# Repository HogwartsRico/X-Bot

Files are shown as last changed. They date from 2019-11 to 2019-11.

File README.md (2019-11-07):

# X-Bot
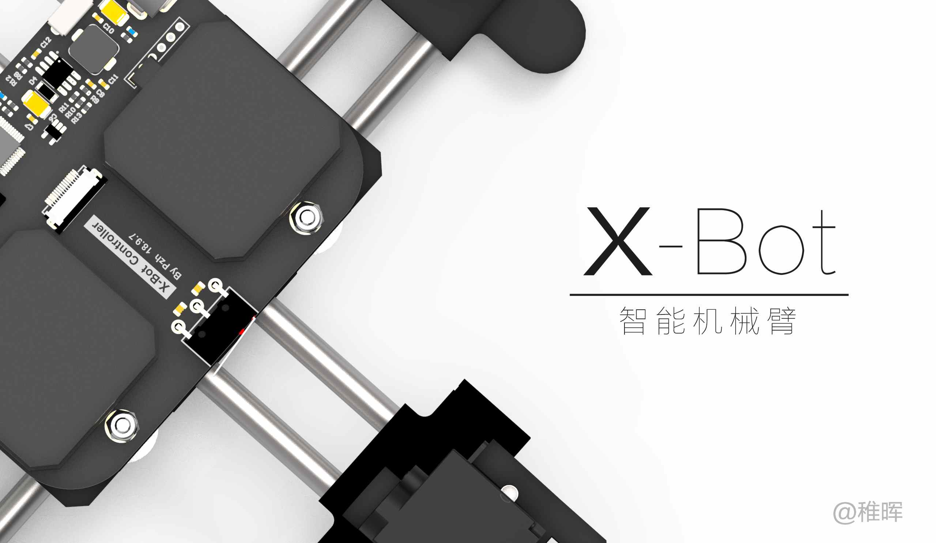
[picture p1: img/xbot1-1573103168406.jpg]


这是一个自己设计的超迷你写字机器人，软件、电路、结构完全开源。

## 前言

关于相信机械臂大家应该都了解过，小到3D打印机、激光雕刻机，大到工厂里使用的工业机械臂，都是机械臂控制的典型应用。随着工业4.0时代的到来，机械臂这样一类最典型的“机器人”，正在逐渐服务于我们生活的方方面面。

X-Bot就是这样一个机械臂作品，确切地说它是我另一个AI项目的先导作品，由于之前看paper发现一个很有趣的条件生成式对抗网络（CGAN）模型，所以产生了一些脑洞准备动手结合硬件造一个AI灵魂画手。既然是画手，光有AI算法当然还不够传神，所以X-Bot就应运而生了，当时也考虑过好几种机械臂方案，最终选择了CoreXY结构作为X-Bot的设计方案。

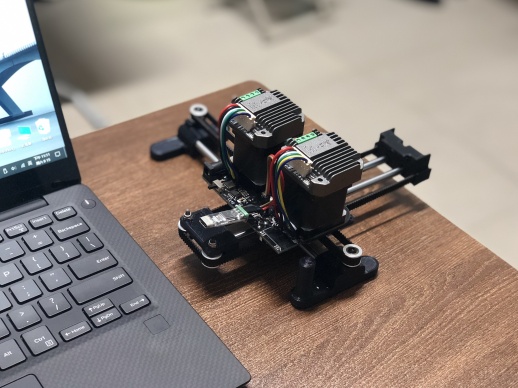
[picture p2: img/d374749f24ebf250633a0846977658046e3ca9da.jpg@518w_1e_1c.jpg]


## 关于机械臂

那么CoreXY结构是什么东西呢？

首先我们来了解一下目前比较流行的机械臂结构有哪些：

> 最经典的XYZ结构

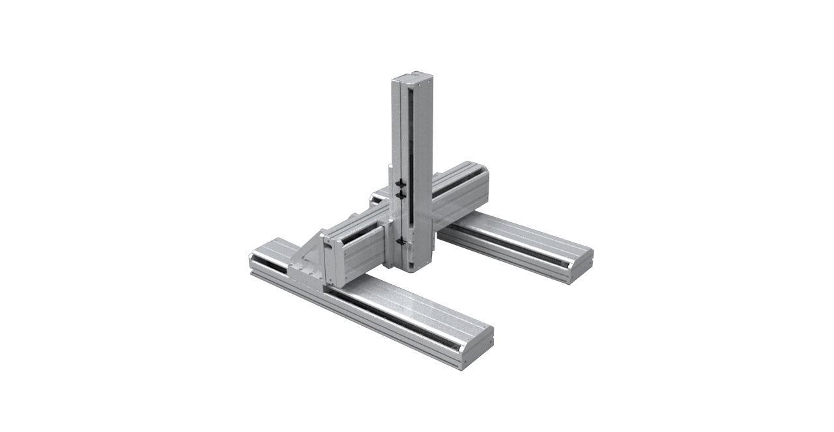
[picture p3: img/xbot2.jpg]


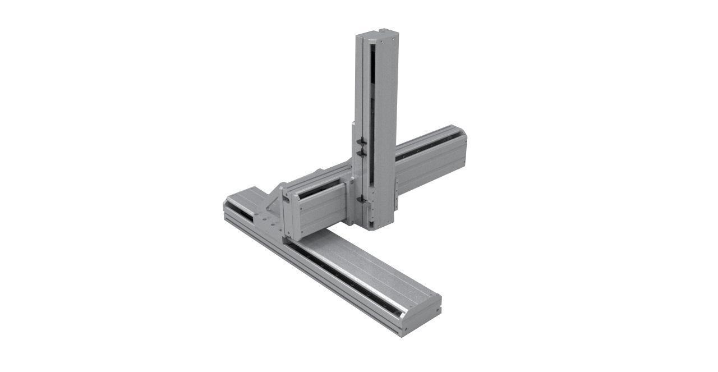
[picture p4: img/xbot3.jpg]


这一类结构大家应该一眼就能看明白是怎么回事，简单说就是在X、Y、Z三个方向上都是独立的直线运动，虽然形式有多种比如图中的第一种被称作龙门式，一般在雕刻机领域用的很多；而第二种在比较追求小型化的3D打印机上经常可以看到其身影。

XYZ结构的好处就结构非常简单，控制也很简单，由于三个方向上的运动都是解耦的（一个方向的运动不会影响到另一个方向），而且相对来说由于是纯线性驱动，其运动精度会比较容易控制。

> DELTA结构

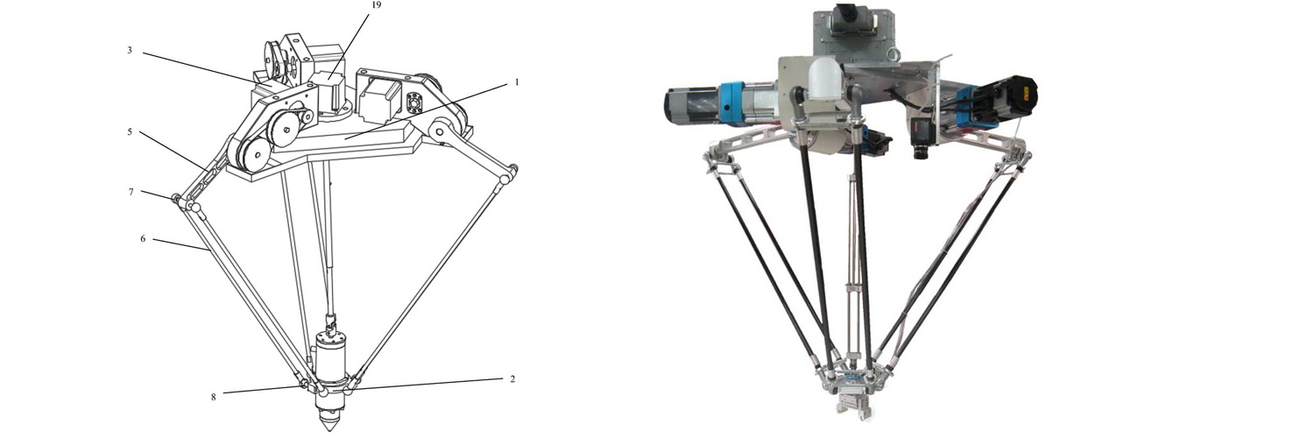
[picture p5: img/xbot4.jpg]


由于我们身处三维空间，因此来说只要是三个*线性独立*的向量都可以用来表征空间中一个唯一的坐标，对应于机械臂中，就是说只要我有三个可以精确驱动控制的电机，我就可以玩出各种花样让一个机械臂精确地运动到某一点。在XYZ结构中，X、Y、Z三个电机的地位并不是对等的，而DELTA结构则以一种很巧妙的方式完全对称地放置三个电机，如上图所示。通过三根连杆两端一共六个万向关节的约束，DELTA机械臂的末端可以运动到三维空间中的任意一点（在行程范围内，且行程空间并不是和XYZ结构一样的一个立方体），这种结构的好处就是非常的**炫酷**，哈哈，其实几年前个人最早决定设计自己的3D打印机的时候，就对DELTA结构非常的热衷~由于杠杆效应，一般来说这类机械臂的运行速度都要比XYZ要快一些，同时由于非线性控制坐标解算需要消耗更多的计算资源，有兴趣的同学可以去了解一下DELTA结构到XYZ坐标的解算公式推导过程。

> 圆柱结构

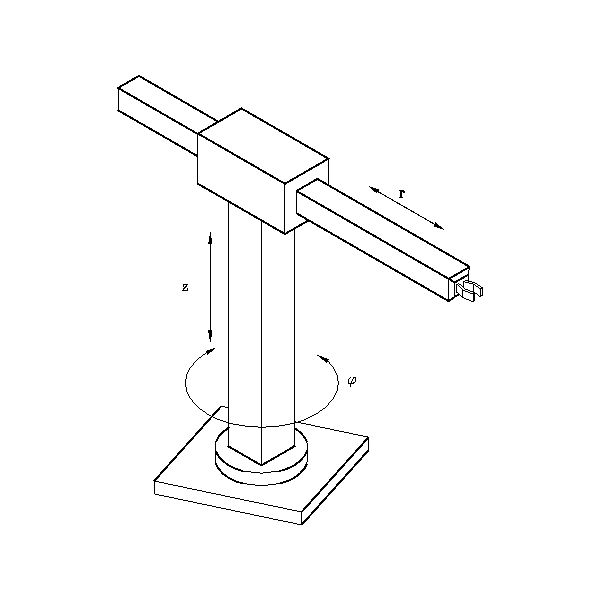
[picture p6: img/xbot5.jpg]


提到XYZ大家首先想到的是笛卡尔坐标系，然而我们在中学的时候就学过另一种坐标系叫极坐标系，也就是用一个角度和一个长度就可以表征平面内一个点的坐标，而且其跟XY坐标的转换也很方便。那么讲极坐标系再加上一个Z轴的直线运动，就得到了这样的圆柱结构机械臂。这类机械臂在实际应用中见到的比较少，因为同为极坐标结构，下面这种SCARA结构有着更“拟人”的效果。

> SCARA结构

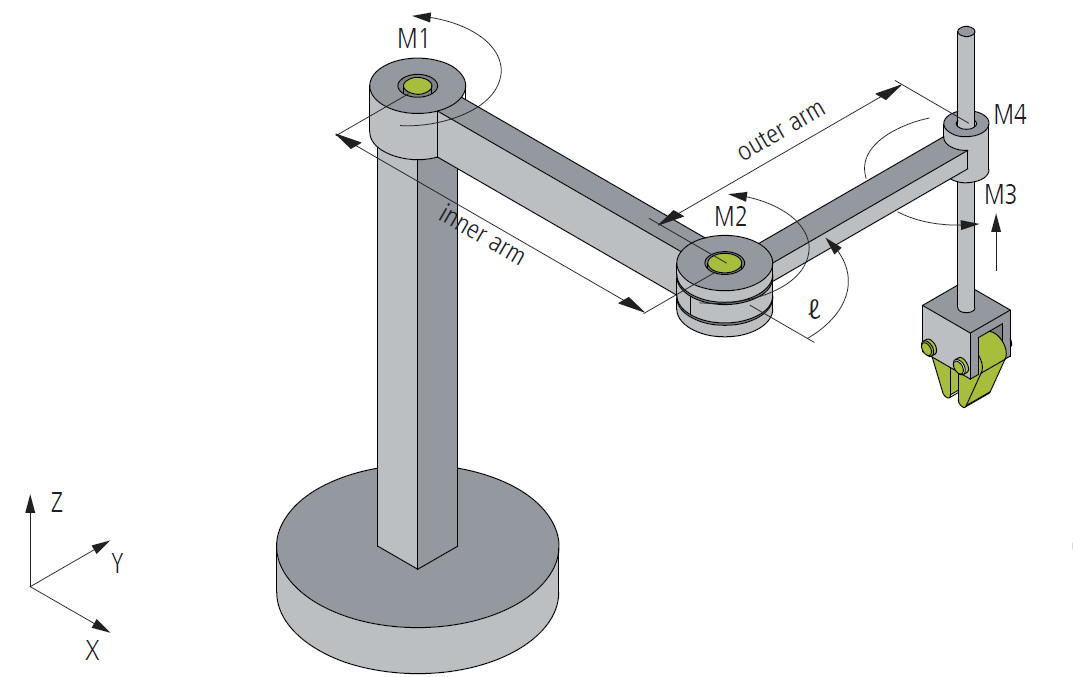
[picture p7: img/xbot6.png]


这一类机械臂的结构非常像人类手臂（虽然自由度差了很多，人手臂应该是7个自由度），优点很明显就是节省空间，缺点也很明显，由于远端的误差放大作用，对于电机角度控制的精度要求非常高，电机的一点点抖动传递到末端都可能造成很大的误差，因此在工业机械臂中，这类机械臂一般都是使用传动误差极小的谐波减速器。

> CoreXY结构

其实关于机械臂的结构还有各种各样，结构设计师们的脑洞实在是让人叹为观止，有兴趣的小伙伴可以去google一下国外的各种3D打印机作品，非常的有意思。这里只最后介绍一下X-Bot中采用的CoreXY结构。

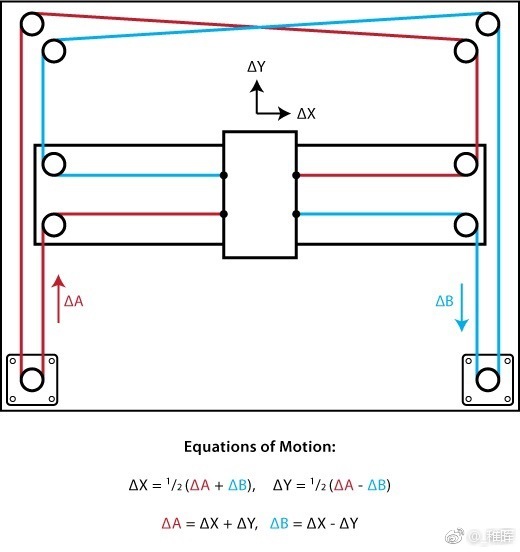
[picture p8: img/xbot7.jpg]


与传统XY结构不同，CoreXY是一种仅使用一根同步带就可以控制末端在XY两个方向运动的结构，非常巧妙；但是和绝大多数其他结构一样，CoreXY这种结构也会有电机和限位开关分散分布，电路连接走线比较麻烦的缺点；于是在其基础上，X-Bot改变了电机放置的位置，将其由两边放置改为中央放置，所有的电路板和电机集中布置，结构更紧凑。

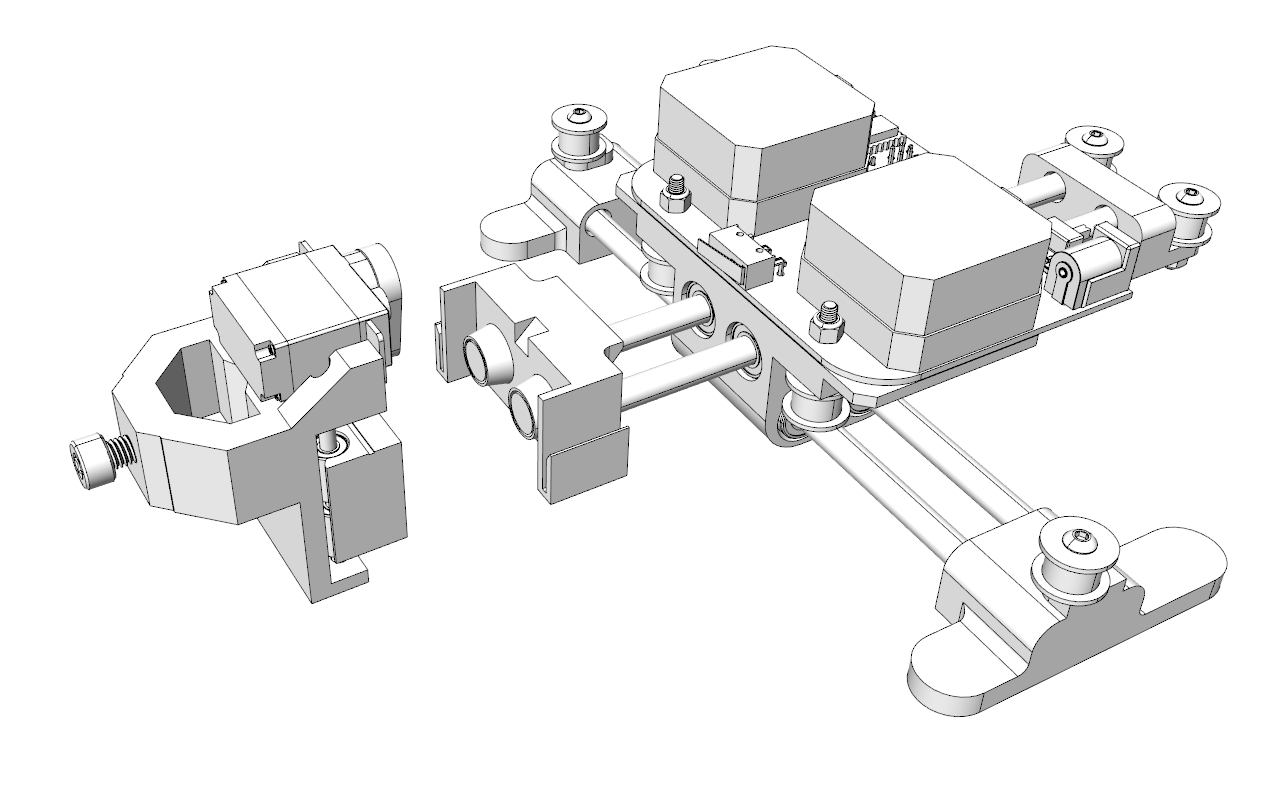
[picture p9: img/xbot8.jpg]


## 电路设计篇

电路很简单就是一个STM32的最小系统，电机驱动直接使用了一体式的驱动器，可以tb搜索一下有很多。蓝牙模块使用的是HC-05，12V供电就行。

## 固件篇

直接移植了Arduino上面很成熟的grbl固件到STM32上，参数都已经设置好了，也把坐标转换函数从XY改为了CoreXY，keil直接烧录就能用了。

## 其他

待更新。

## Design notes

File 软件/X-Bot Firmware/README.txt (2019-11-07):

【SOL开源】GRBL-0.9j-for-STM32

--------------------------------------------------------
1.移植说明：

移植平台：STM32F103C8T6
移植GRBL版本：0.9j.20160726

当前状态：
（1）所有已经调试通过，无warning；
（2）所有部件可以正常运行，并经过实机测试。

--------------------------------------------------------
2.资源使用：

（1）引脚（具体可参考cpu_map_stm32f10x.h文件）

步进电机-X轴脉冲	：	GPIOB5
步进电机-Y轴脉冲	：	GPIOB6
步进电机-Z轴脉冲	：	GPIOB7
步进电机-X轴方向	：	GPIOB8
步进电机-Y轴方向	：	GPIOB9
步进电机-Z轴方向	：	GPIOB10
步进电机-使能		：	GPIOB11
冷却-FLOOD		：	GPIOB3	
冷却-MIST（M7）		：	GPIOB4
主轴-PWM		：	GPIOA0
主轴-使能		：	GPIOA1
主轴-方向		：	GPIOA2
G38探测器		：	GPIOA4
系统-复位		：	GPIOA5
系统-给进保持		：	GPIOA6
系统-循环开始		：	GPIOA7
系统-安全门		：	GPIOA8
串口-TX			：	GPIOA9
串口-RX			：	GPIOA10
限位-X轴		：	GPIOA11
限位-Y轴		：	GPIOA12
限位-Z轴		：	GPIOA15
调试-SWDIO		：	GPIOA13
调试-SWCLK		：	GPIOA14

空闲			：	GPIOA3，GPIOB0，GPIOB1
空闲-SPI		：	GPIOB12，GPIOB13，GPIOB14，GPIOB15

（2）存储器
ROM（无优化）		：	43.22kB
FLASH做为EEPROM		：	1kB（可自由调整）

2017-4-8
SOL.lab
MaxwellXyao
Email:917286114@qq.com

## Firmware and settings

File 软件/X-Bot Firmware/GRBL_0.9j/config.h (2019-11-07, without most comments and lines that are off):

#define config_h
#include "grbl.h" // For Arduino IDE compatibility.
#define DEFAULTS_GENERIC
#define BAUD_RATE 115200
#define CPU_MAP_STM32F10X // Stm32f10x
#define CMD_STATUS_REPORT '?'
#define CMD_FEED_HOLD '!'
#define CMD_CYCLE_START '~'
#define CMD_RESET 0x18 // ctrl-x.
#define CMD_SAFETY_DOOR '@'
#define HOMING_INIT_LOCK // Comment to disable
#define HOMING_CYCLE_0 (1<<X_AXIS)
#define HOMING_CYCLE_1 (1<<Y_AXIS)
#define N_HOMING_LOCATE_CYCLE 1 // Integer (1-128)
#define N_STARTUP_LINE 2 // Integer (1-2)
#define N_DECIMAL_COORDVALUE_INCH 4 // Coordinate or position value in inches
#define N_DECIMAL_COORDVALUE_MM   3 // Coordinate or position value in mm
#define N_DECIMAL_RATEVALUE_INCH  1 // Rate or velocity value in in/min
#define N_DECIMAL_RATEVALUE_MM    0 // Rate or velocity value in mm/min
#define N_DECIMAL_SETTINGVALUE    3 // Decimals for floating point setting values
#define MESSAGE_PROBE_COORDINATES // Enabled by default. Comment to disable.
#define SAFETY_DOOR_SPINDLE_DELAY 4000
#define SAFETY_DOOR_COOLANT_DELAY 1000
#define COREXY // Default disabled. Uncomment to enable.
#define ACCELERATION_TICKS_PER_SECOND 100
#define ADAPTIVE_MULTI_AXIS_STEP_SMOOTHING  // Default enabled. Comment to disable.
#define TOOL_LENGTH_OFFSET_AXIS Z_AXIS // Default z-axis. Valid values are X_AXIS, Y_AXIS, or Z_AXIS.
#define VARIABLE_SPINDLE // Default enabled. Comment to disable.
#define SPINDLE_MAX_RPM 1000.0 // Max spindle RPM. This value is equal to 100% duty cycle on the PWM.
#define SPINDLE_MIN_RPM 0.0    // Min spindle RPM. This value is equal to (1/256) duty cycle on the PWM.
#define MINIMUM_JUNCTION_SPEED 0.0 // (mm/min)
#define MINIMUM_FEED_RATE 1.0 // (mm/min)
#define N_ARC_CORRECTION 12 // Integer (1-255)
#define ARC_ANGULAR_TRAVEL_EPSILON 5E-7 // Float (radians)
#define DWELL_TIME_STEP 50 // Integer (1-255) (milliseconds)
#define HARD_LIMIT_FORCE_STATE_CHECK // Default disabled. Uncomment to enable.
#if defined(USE_SPINDLE_DIR_AS_ENABLE_PIN) && !defined(VARIABLE_SPINDLE)
  #error "USE_SPINDLE_DIR_AS_ENABLE_PIN may only be used with VARIABLE_SPINDLE enabled"
#endif
#if defined(USE_SPINDLE_DIR_AS_ENABLE_PIN) && !defined(CPU_MAP_ATMEGA328P)
  #error "USE_SPINDLE_DIR_AS_ENABLE_PIN may only be used with a 328p processor"
#endif

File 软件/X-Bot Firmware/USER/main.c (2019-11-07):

#include "project_include.h"
#include "grbl.h"

// Declare system global variable structure
system_t sys; 


int main(void)
{		
	JTAG_Set(SWD_ENABLE);			//JTAG接口状态设置
	delay_init(); 					//延时初始化

	// Initialize system upon power-up.
	serial_init();   // Setup serial baud rate and interrupts
	settings_init(); // Load Grbl settings from EEPROM
	stepper_init();  // Configure stepper pins and interrupt timers
	system_init();   // Configure pinout pins and pin-change interrupt
	
	memset(&sys, 0, sizeof(system_t));  // Clear all system variables
	sys.abort = true;   // Set abort to complete initialization
	sei(); // Enable interrupts
	
	// Check for power-up and set system alarm if homing is enabled to force homing cycle
	// by setting Grbl's alarm state. Alarm locks out all g-code commands, including the
	// startup scripts, but allows access to settings and internal commands. Only a homing
	// cycle '$H' or kill alarm locks '$X' will disable the alarm.
	// NOTE: The startup script will run after successful completion of the homing cycle, but
	// not after disabling the alarm locks. Prevents motion startup blocks from crashing into
	// things uncontrollably. Very bad.
#ifdef HOMING_INIT_LOCK
	if (bit_istrue(settings.flags,BITFLAG_HOMING_ENABLE)) { sys.state = STATE_ALARM; }
#endif
	
	// Force Grbl into an ALARM state upon a power-cycle or hard reset.
#ifdef FORCE_INITIALIZATION_ALARM
	sys.state = STATE_ALARM;
#endif
	
	// Grbl initialization loop upon power-up or a system abort. For the latter, all processes
	// will return to this loop to be cleanly re-initialized.
	for(;;) 
	{

	    // TODO: Separate configure task that require interrupts to be disabled, especially upon
	    // a system abort and ensuring any active interrupts are cleanly reset.
	  
	    // Reset Grbl primary systems.
	    serial_reset_read_buffer(); // Clear serial read buffer
	    gc_init(); // Set g-code parser to default state
	    spindle_init();
	    coolant_init();
	    limits_init(); 
	    probe_init();
	    plan_reset(); // Clear block buffer and planner variables
	    st_reset(); // Clear stepper subsystem variables.
	
	    // Sync cleared gcode and planner positions to current system position.
	    plan_sync_position();
	    gc_sync_position();
	
	    // Reset system variables.
	    sys.abort = false;
	    sys_rt_exec_state = 0;
	    sys_rt_exec_alarm = 0;
	    sys.suspend = false;
	    sys.soft_limit = false;
		
	              
	    // Start Grbl main loop. Processes program inputs and executes them.
	    protocol_main_loop();
	}
}

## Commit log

2019-11-07 初始化仓库
    [X-Bot.PcbDoc, X-Bot.PrjPCB, X-Bot.SchDoc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]
2019-11-07 添加img文件夹

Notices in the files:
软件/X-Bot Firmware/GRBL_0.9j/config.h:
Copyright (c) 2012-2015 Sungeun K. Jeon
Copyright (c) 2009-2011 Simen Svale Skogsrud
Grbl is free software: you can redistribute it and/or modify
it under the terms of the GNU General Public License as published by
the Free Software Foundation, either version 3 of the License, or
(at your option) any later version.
